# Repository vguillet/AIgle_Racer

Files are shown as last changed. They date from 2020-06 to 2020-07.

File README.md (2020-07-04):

# AIgle Racer Project

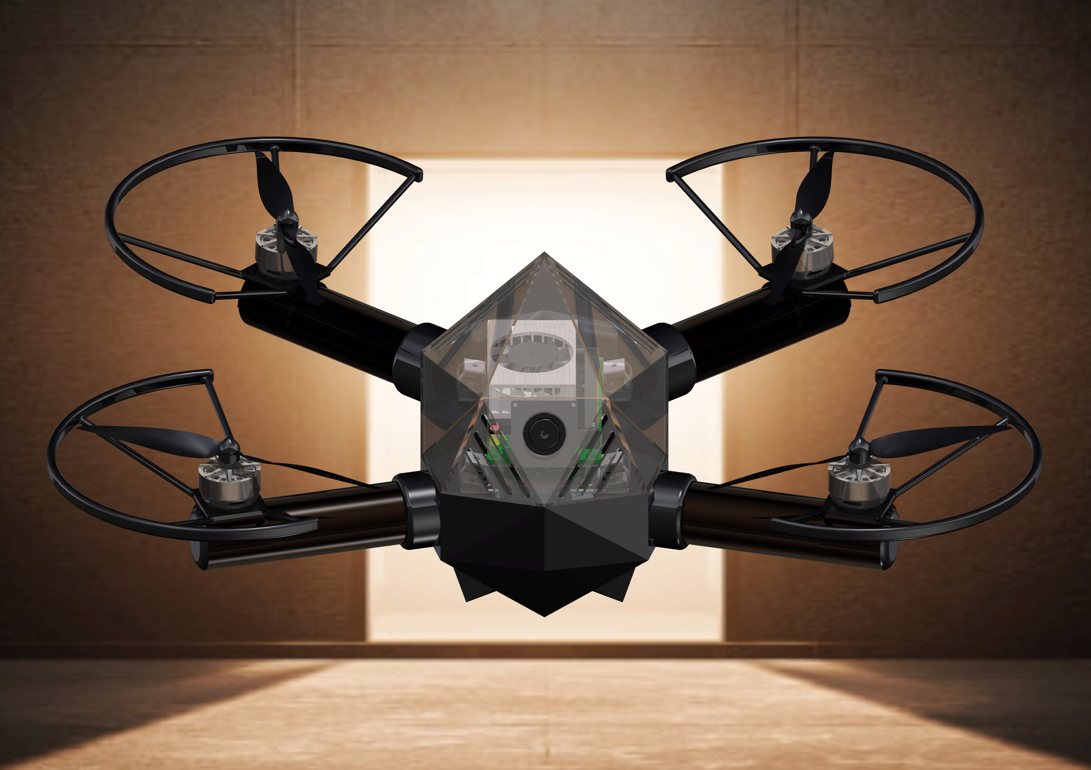
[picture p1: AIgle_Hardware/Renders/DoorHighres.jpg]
cover


> This project was developed during the 2019-2020 Fall DSE as part of the **TU Delft Aerspace Engineering Bachelor**.

> This project was undertaken with the intention of paving the way to future drone racing endeavor, and facilitate AI research and development.

> The design team consists of eleven Bachelor students working full time for 10 weeks. 

Drone racing has gathered increasing attention and interest in the past few years, establishing itself as a sport on par with more traditional ones such as Formula 1. A subset of it, autonomous drone racing, has been growing rapidly in popularity, recently capturing the interest of both the industry, the general public, and the scientific community. Since its beginning in 2016 with the IROS Autonomous Drone Race, the number of competitions have expanded, with more industry players such as the Drone Racing League (DRL) hosting its own competition in 2019, to fully virtual drone races being held by NeurIPS (also in 2019). 

The essence of these competition has however remained the same. Teams compete to develop the most effective software to pilot a standardised drone as quickly as possible over a given circuit. The drone being standardised is a critical aspect of the competition, as it ensures that the software is the sole deciding factor. During the DRL races, the competition host provided the drones competitors would be flying, ensuring this way that no drone had a mechanical advantage over its opponents. This however brings about a number of issues. The cost of hosting a competition goes up drastically, as the cost of producing, maintaining, and repairing the drones then becomes the responsibility of the host. It also means competitors would not be able to effectively test, adjust, and optimise their algorithms prior to the race, reducing the teams' potential ability to compete. In an effort to alleviate these issues, group 19 of the TU Delft 2020 DSE aims to propose an open-source hardware solution for race organizers and teams to be used in future autonomous drone racing competitions. The end goal of the project is to facilitate a worldwide collaboration on the development of artificial intelligence in agile autonomous drone flight. 

This repository contains all the information and results necessary to get started with the AIgle Racer platform. 

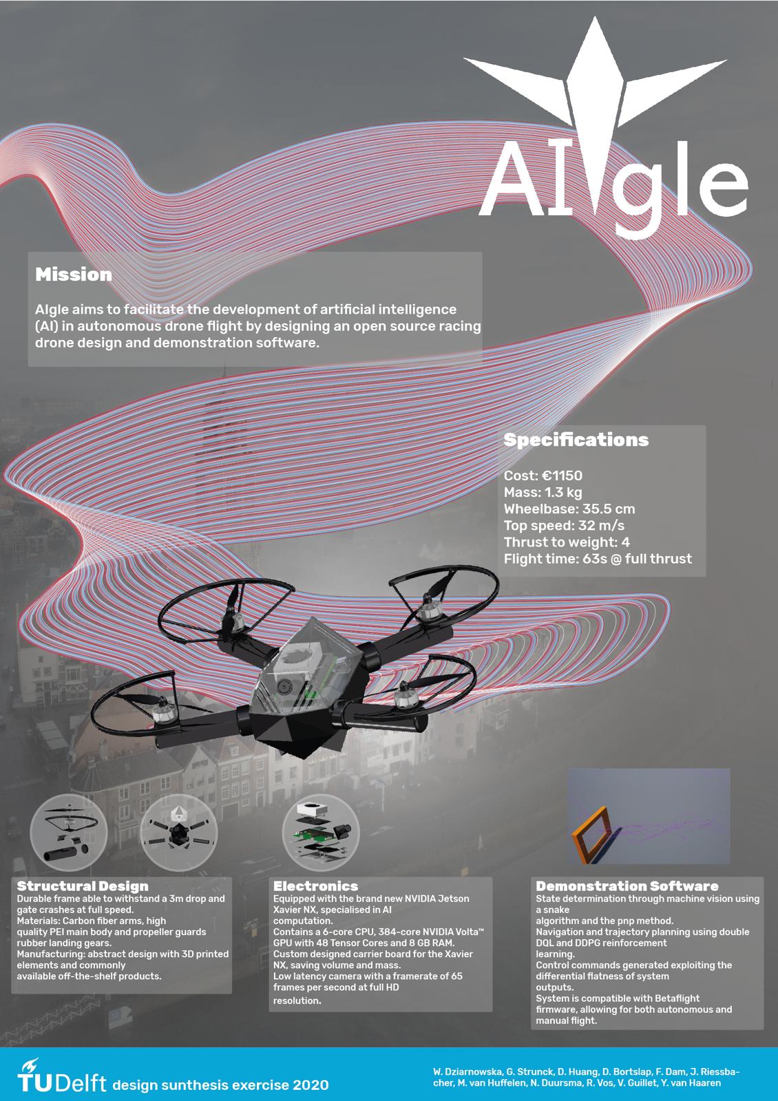
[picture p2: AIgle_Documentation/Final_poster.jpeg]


## AIgle Documentation

The AIgle Racer is documented in four distinct reports, each compiled at various stages of progress of the project.
  - Project plan: Depicts the initial organisation of the project
  - Baseline report: Describes the structuration of the research and development based on preliminary research,
  - Mid-term report: Explains the concepts elaboration and evaluation
  - Final report: Contains the detailed design, with the fully developed concept and instructions based on in-depth research.

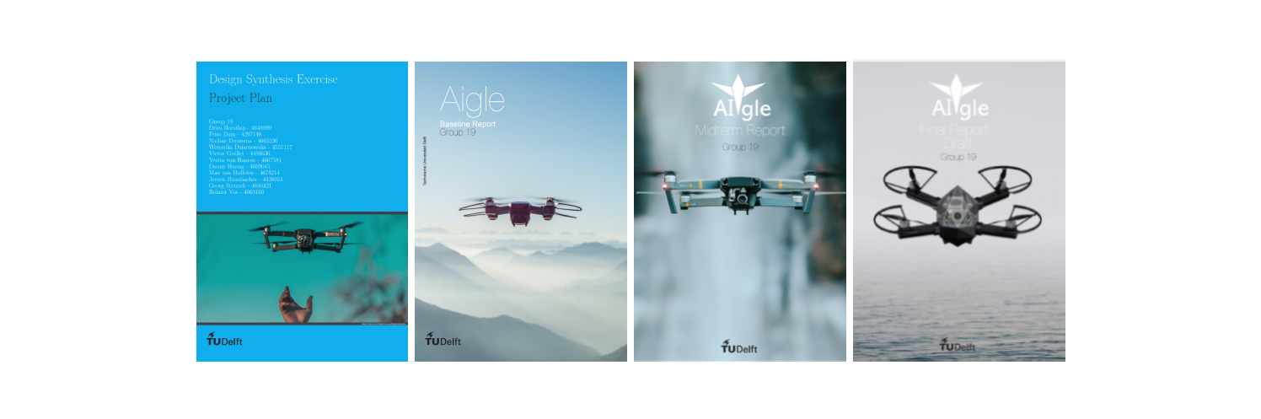
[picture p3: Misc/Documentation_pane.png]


## AIgle Hardware
The AIgle hardware folder contains all the information necessary for the production and assembly of the AIgle drone. To guide and facilitate the production, the following are provided:

  - Parts lists
  - 3D Catia models
  - Custom PCB diagrams and description
  
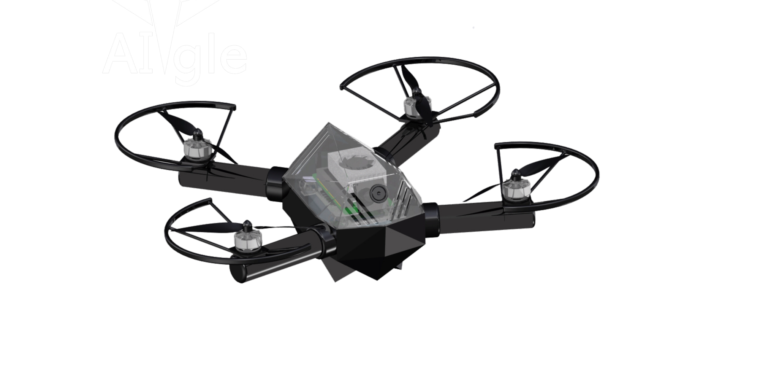
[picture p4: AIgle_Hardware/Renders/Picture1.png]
  

## AIgle Software
> Note: The AIgle demonstration software can be found in AIgle_Project/src

The AIgle Project src file contains all the demonstrations software provided to act as a baseline for building autonomous racing software to use with the AIgle racer platform. A general suggested pipeline is available in the documentation along with the result of research performed on the various methods and approach demonstrated.
  - Machine Vision & State estimation: Focus on retrieving and processing sensor data to get an estimate of the position of the drone in 3D space
  - Navigation: Focus on determining the path and trajectories to be followed by the drone during the race.
  
    Algorithms available: **DDQN**, **DDPG**
    
    The navigation uses [Airsim](https://github.com/microsoft/AirSim) as training and testing environment
    
  - Control & stability: Focus on translating the desired drone movement (control position, velocities, attitude) into commands (subsequenctly sent to an electronic speed controller) 

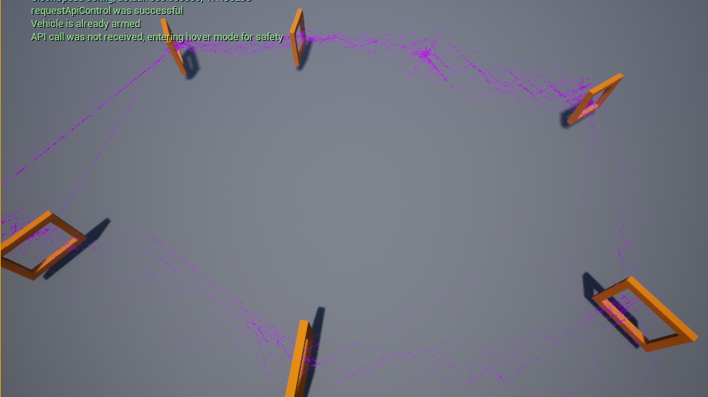
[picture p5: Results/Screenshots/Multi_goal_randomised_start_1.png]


## AIgle Concept Development Tools
The concept evelopment tool folder contains the code which was used for desiging and sizing the drone. This includes:
  - Propulsion: Contains the tools used to obtain suitable battery/motor/propelor triplets based on different input criterias. Vertification code is also included, to be used with [eCalc](https://ecalc.ch/xcoptercalc.php)
  - Structures:

## Acknowledgement
The group would like to extend special thanks to Ir. C. De Wagter for his tremendous insight into drone racing, and for sharing his knowledge and experience in drone racing design. The group would also like to thank B. Mercier and Y. Zhang for their valuable advices and help during the design phase, and D. Martini for his important input throughout the project. The tutors and coaches have been present throughout the entire development of the project, and their contribution has proven essential to its success.

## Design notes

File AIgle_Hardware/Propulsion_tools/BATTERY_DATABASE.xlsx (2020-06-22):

Battery | S_type | Capacity [mAh] | Weight [g] | Predicted weight [g] | Difference^2 | Cost ($) | Predicted cost [g] | Difference^2 | C-rating | Amps (=Cap*C) | Note | Source
1 | 4S | 2600 | 273 | 281.04 | 64.6416 | 36.06 | 27.668 | 70.425664 | 80 | 208 | From UK | https://www.hobbyrc.co.uk/gnb-2600mah-4s-80c-lipo-battery
2 | 4S | 3000 | 324 | 313 | 121 | 22.66 | 30.48 | 61.1524 | 30 | 90 |  | https://www.banggood.com/nl/ZOP-Power-14_8V-3000mah-30C-4S-Lipo-Battery-XT60-Plug-for-RC-Quadcopter-p-1237191.html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
3 | 4S | 2600 | 298 | 281.04 | 287.6416 |  | 27.668 | 765.518224 | 80 | 208 | No price info | https://www.amazon.com/RoaringTop-Battery-2600mAh-14-8V-Airplane/dp/B01LYZQE5S
4 | 4S | 2200 | 247 | 249.08 | 4.3264 | 31.06 | 24.856 | 38.489616 | 110 | 242 | From UK | https://www.hobbyrc.co.uk/gnb-2200mah-4s-110c-lipo-battery
5 | 4S | 4000 | 435 | 392.9 | 1772.41 | 34.61 | 37.51 | 8.41 | 60 | 240 |  | https://www.banggood.com/nl/ZOP-Power-14_8V-4000mAh-4S-60C-Lipo-Battery-XT60-Plug-p-1104628.html?gpla=1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

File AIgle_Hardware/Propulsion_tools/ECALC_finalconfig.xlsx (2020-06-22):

eCalc - Multicopter Calculator all data without guarantee - Accuracy: /-15%
Project Name |  | FINALCONFIG
Battery |  | custom
Configuration: |  | 4S1P
Load: | C | 44.70
Voltage: | V | 13.44
Rated Voltage: | V | 14.80
Energy: | Wh | 53.28
Total Capacity: | mAh | 3600
max. discharge: |  | 80%
Used Capacity: | mAh | 2880
min. Flight Time: | min | 1.1
Mixed Flight Time: | min | 5.8
Hover Flight Time: | min | 9.7
Weight: | g | 352
 | oz | 12.4
Controller |  | custom
Current: | A cont. | 45
 | A max | 45
Weight: | g | 4.5
 | oz | 0.2
Accessories
Current drain: | A | 2
Weight: | g | 237
 | oz | 8.4
Motor @ Maximum |  | EMAX Eco 2306-2400 (2400)
Gear Ratio: | : 1 | 1
Weight: | g | 28
 | oz | 1
Current: | A | 39.73
Voltage: | V | 13.20
Revolutions*: | rpm | 26806
electric Power: | W | 524.3
mech. Power: | W | 424.6
Efficiency: | % | 81.0
est. Temperature: | °C | 64
 | °F | 147
Motor @ Hover
Propeller |  | APC Electric E (0°) 6" x 4"
# Blades: |  | 2
avail.Thrust @ | @
 | @
Current: | A | 3.95
Voltage: | V | 15.41
Revolutions*: | rpm | 11765
Throttle (log): | % | 22
Throttle (linear): | % | 35
Power-Weight: | W/kg | 198.6
 | W/lb | 90.1
Efficiency: | % | 82.3
specific Thrust: | g/W | 5.13
 | oz/W | 0.18
est. Temperature: | °C | 29
 | °F | 84
Total Drive
Drive Weight: | g | 530
 | oz | 18.7
Power-Weight: | W/kg | 1681.5
 | W/lb | 762.7
Thrust-Weight: | : 1 | 4.2
Current @ Hover: | A | 15.79
P(in) @ Hover: | W | 247.7
P(out) @ Hover: | W | 200.2
Efficiency @ Hover: | % | 80.8
Current @ max: | A | 158.91
P(in) @ max: | W | 2493.0
P(out) @ max: | W | 1698.3
Efficiency @ max: | % | 68.1
Multicopter
# of Rotors: |  | 4 - flat
All-up Weight: | g | 1247
 | oz | 44
add. Payload: | g | 3229
 | oz | 113.9
max Tilt: | ° | 74
max. Speed: | km/h | 166
 | mph | 103.1
est. Range: | m | 4374
 | mi | 2.72
est. rate of climb: | m/s | 28.4
 | ft/min | 5591
Total Disc Area: | dm² | 7.30
 | in² | 113.15
with Rotor fail: |  | uncontrolable
Remarks: |  | 0
(c) by Solution for All - 7.20.010, 13.5.2020

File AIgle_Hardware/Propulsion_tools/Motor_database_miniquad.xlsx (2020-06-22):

Name | TESTED_KV | motor_weight(g) | Prop_Tested(100) | T_Max(g) | T_avg_max(g) | I_max(A) | I_avg_max(A) | Volt_avg_min | Volt_max | RPM_max | RPM_min | RPM_avg_max | Watts | T/W(g/W) | Prop(IDLE) | Thrust(g)(IDLE) | Amps(IDLE) | Volts(IDLE) | RPMs(IDLE) | Watts(IDLE) | T/W(g/W)(IDLE)
Karearea Toa 2207 2650kv | 2700 | 33.8 | HQ v1s 5x4x3 | 1508.00 | 1480.00 | 161.52 | 41.82 | 15.45 | 16.16 | 36014.00 | 34423.00 | 34925.00 | 646.00 | 2.30 | HQ v1s 5x4x3 | 46.00 | 0.99 | 16.13 | 6298.00 | 16.00 | 2.90
Karearea Toa 2207 2650kv | 2700 | 33.8 | Lumenier 5x4.5 | 1552.00 | 1537.00 | 181.45 | 46.00 | 15.35 | 16.16 | 35714.00 | 33094.00 | 33552.00 | 706.00 | 2.20 | Lumenier 5x4.5 | 48.00 | 0.85 | 16.12 | 6311.00 | 14.00 | 3.50
Karearea Toa 2207 2650kv | 2700 | 33.8 | DAL Cyclone 5x4x3 | 1556.00 | 1537.00 | 175.11 | 46.66 | 15.37 | 16.16 | 34843.00 | 32840.00 | 33378.00 | 717.00 | 2.10 | DAL Cyclone 5x4x3 | 45.00 | 0.96 | 16.13 | 6326.00 | 15.00 | 2.90
Karearea Toa 2207 2650kv | 2700 | 33.8 | HQ 5x4x3GF | 1608.00 | 1595.00 | 180.16 | 48.57 | 15.34 | 16.16 | 34843.00 | 32345.00 | 32867.00 | 745.00 | 2.10 | HQ 5x4x3GF | 59.00 | 1.08 | 16.13 | 6289.00 | 17.00 | 3.40
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

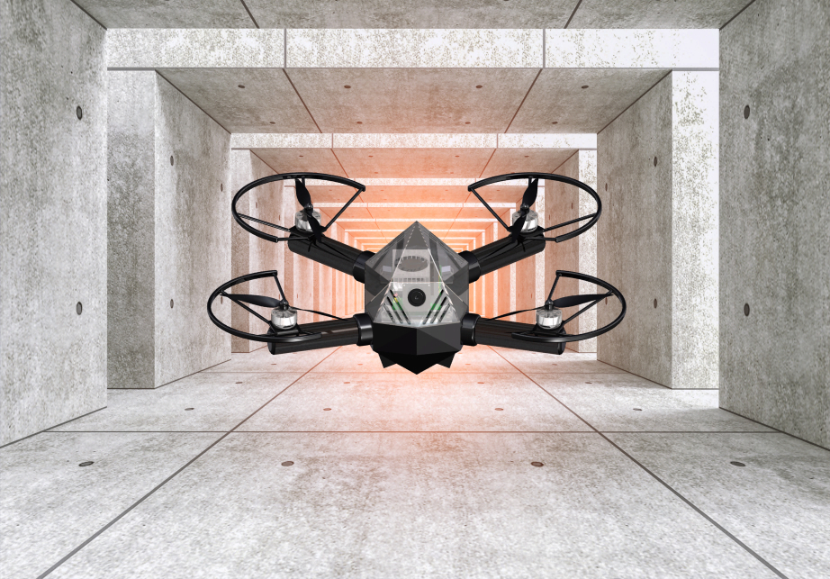
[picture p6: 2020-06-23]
AIgle_Hardware/Renders/Gates3.jpg

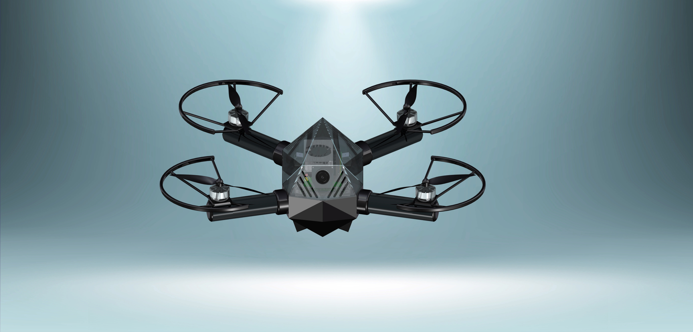
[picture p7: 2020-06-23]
AIgle_Hardware/Renders/Grey2.jpg

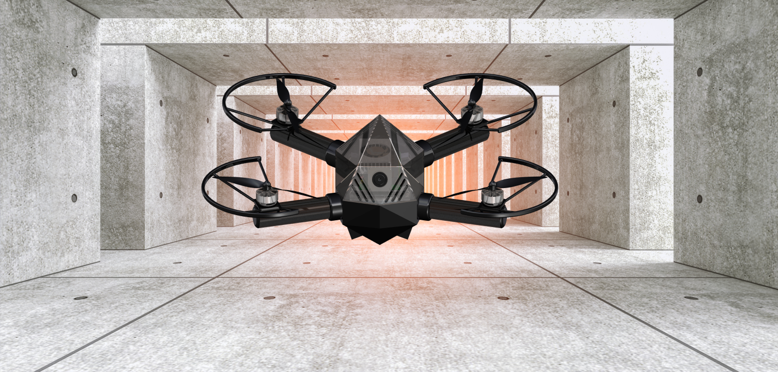
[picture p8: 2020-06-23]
AIgle_Hardware/Renders/Gates.png

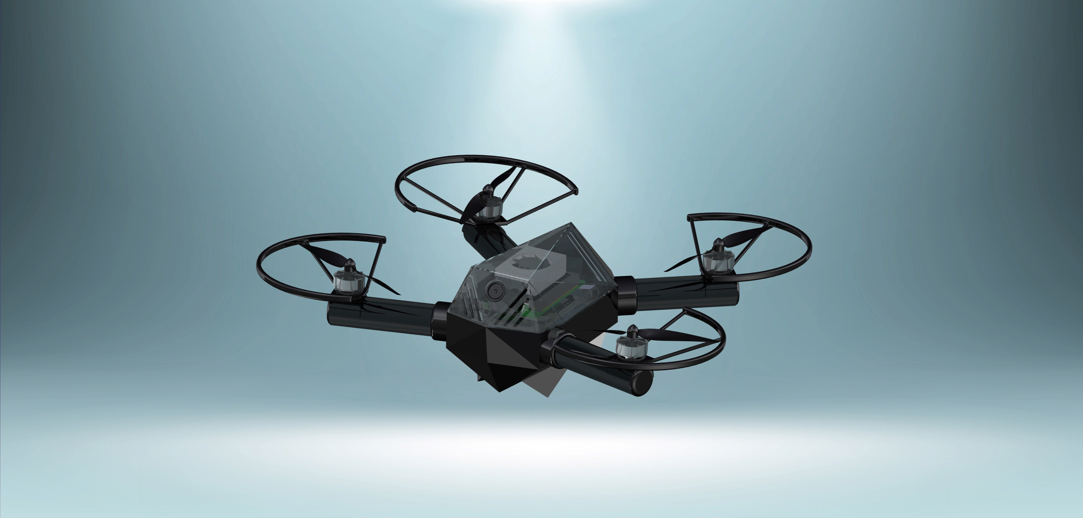
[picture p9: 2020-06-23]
AIgle_Hardware/Renders/Grey.jpg

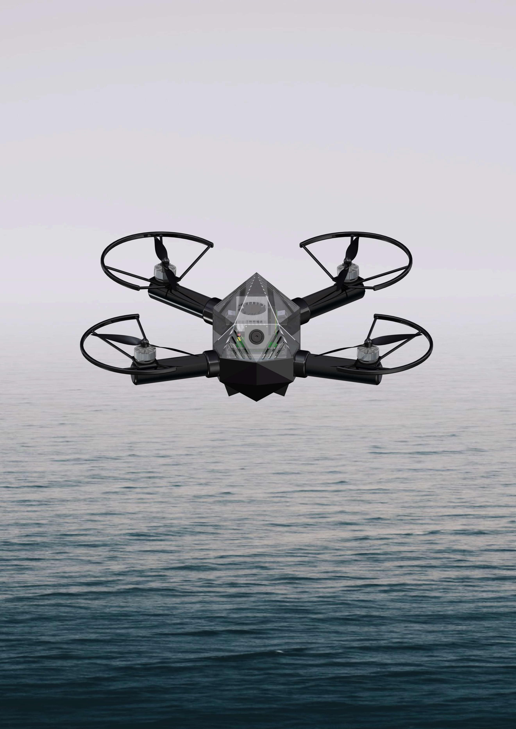
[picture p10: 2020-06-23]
AIgle_Hardware/Renders/Renderfront.jpg

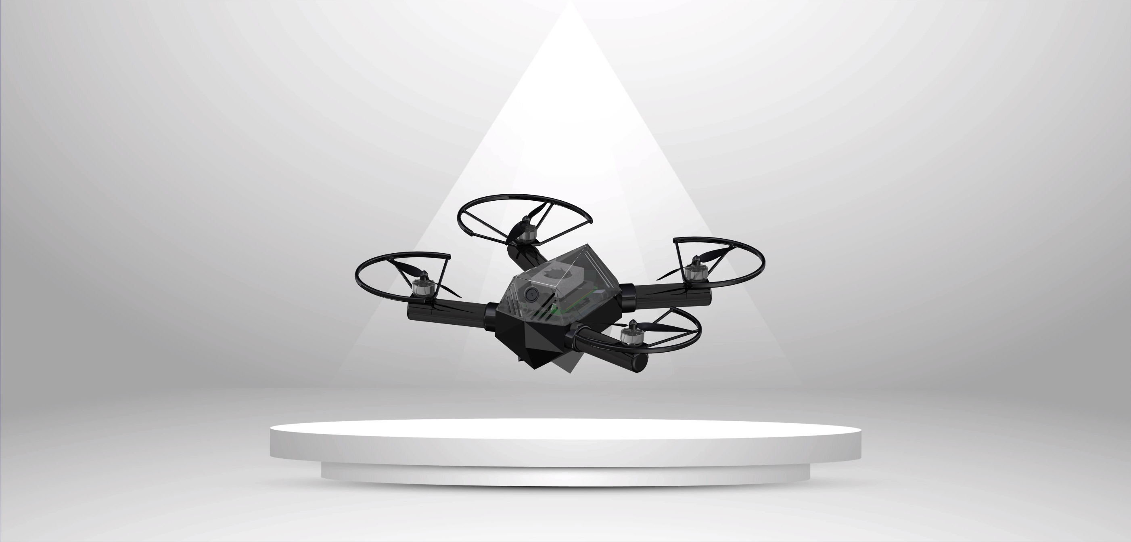
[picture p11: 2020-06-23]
AIgle_Hardware/Renders/platform.jpg

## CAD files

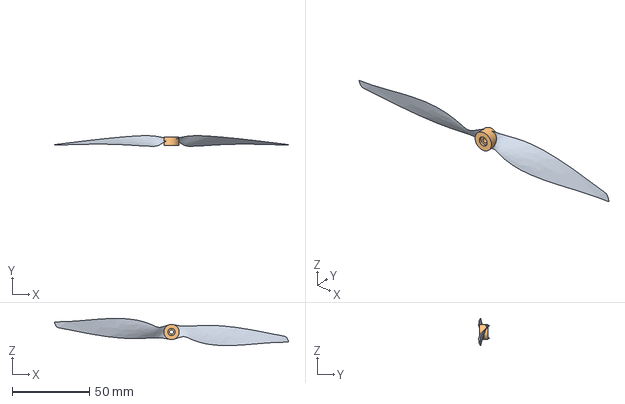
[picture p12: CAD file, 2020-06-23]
AIgle_Hardware/Catia_Models/APC12x6EPPropv1scaled v1.step
151.9 x 6.87 x 17.7 mm

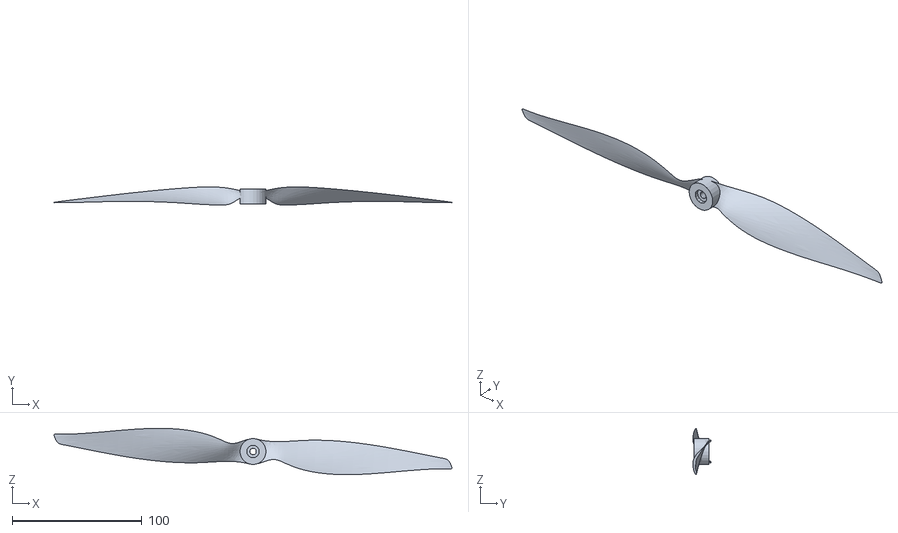
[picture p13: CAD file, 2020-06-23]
AIgle_Hardware/Catia_Models/APC12x6EPProp v1.stl
306.6 x 14.0 x 35.7

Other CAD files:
AIgle_Hardware/Catia_Models/Arm.CATPart
AIgle_Hardware/Catia_Models/AssemblyExploded.CATProduct
AIgle_Hardware/Catia_Models/AssemblyFinal.CATProduct
AIgle_Hardware/Catia_Models/PropDop.CATPart
AIgle_Hardware/Catia_Models/PropGuards.CATPart
AIgle_Hardware/Catia_Models/Propeller.CATPart
AIgle_Hardware/Catia_Models/Reference.CATPart
AIgle_Hardware/Catia_Models/Symmetry of Arm.CATPart
AIgle_Hardware/Catia_Models/Symmetry of Dopje.CATPart
AIgle_Hardware/Catia_Models/Symmetry of LandingGear.CATPart
AIgle_Hardware/Catia_Models/Symmetry of MotorMount.CATPart
AIgle_Hardware/Catia_Models/Symmetry of Product4.CATProduct
AIgle_Hardware/Catia_Models/Symmetry of PropGuards.CATPart

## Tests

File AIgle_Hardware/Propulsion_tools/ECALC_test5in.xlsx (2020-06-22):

eCalc - Multicopter Calculator all data without guarantee - Accuracy: /-15%
Project Name |  | VERI1WIN5in | VERI2WIN5in | VERI3WIN5in
Battery |  | LiPo 3000mAh - 65/100C | LiPo 3000mAh - 65/100C | LiPo 4000mAh - 55/80C
Configuration: |  | 4S1P | 4S1P | 4S1P
Load: | C | 39.77 | 44.02 | 39.05
Voltage: | V | 13.83 | 13.63 | 13.81
Rated Voltage: | V | 14.80 | 14.80 | 14.80
Energy: | Wh | 44.4 | 44.4 | 59.2
Total Capacity: | mAh | 3000 | 3000 | 4000
max. discharge: |  | 80% | 80% | 80%
Used Capacity: | mAh | 2400 | 2400 | 3200
min. Flight Time: | min | 1.2 | 1.1 | 1.2
Mixed Flight Time: | min | 5.7 | 5.6 | 6.8
Hover Flight Time: | min | 9.6 | 9.5 | 11.9
Weight: | g | 336 | 336 | 432
 | oz | 11.9 | 11.9 | 15.2
Controller |  | custom | custom | custom
Current: | A cont. | 45 | 45 | 45
 | A max | 45 | 45 | 45
Weight: | g | 4.5 | 4.5 | 4.5
 | oz | 0.2 | 0.2 | 0.2
Accessories
Current drain: | A | 2 | 2 | 2
Weight: | g | 185 | 185 | 185
 | oz | 6.5 | 6.5 | 6.5
Motor @ Maximum |  | Cobra CP-2207-2300 (2300) | T-Motor F60 PRO III KV2500 (2500) | iFlight XING-E X2306-2450KV (2450)
Gear Ratio: | : 1 | 1 | 1 | 1
Weight: | g | 36 | 35 | 33
 | oz | 1.3 | 1.2 | 1.2
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

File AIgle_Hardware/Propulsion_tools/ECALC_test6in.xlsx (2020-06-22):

eCalc - Multicopter Calculator all data without guarantee - Accuracy: /-15%
Project Name |  | VERI1WIN6in | VERI2WIN6in
Battery |  | LiPo 3000mAh - 65/100C | LiPo 4200mAh - 55/80C
Configuration: |  | 4S1P | 4S1P
Load: | C | 47.75 | 41.63
Voltage: | V | 13.45 | 13.66
Rated Voltage: | V | 14.80 | 14.80
Energy: | Wh | 44.4 | 62.16
Total Capacity: | mAh | 3000 | 4200
max. discharge: |  | 80% | 80%
Used Capacity: | mAh | 2400 | 3360
min. Flight Time: | min | 1.0 | 1.2
Mixed Flight Time: | min | 5.7 | 7.0
Hover Flight Time: | min | 10.4 | 12.5
Weight: | g | 336 | 452
 | oz | 11.9 | 15.9
Controller |  | custom | custom
Current: | A cont. | 40 | 45
 | A max | 40 | 45
Weight: | g | 4.5 | 4.5
 | oz | 0.2 | 0.2
Accessories
Current drain: | A | 2 | 2
Weight: | g | 185 | 185
 | oz | 6.5 | 6.5
Motor @ Maximum |  | Cobra CP-2207-2450 (2450) | iFlight XING-E X2306-2450KV (2450)
Gear Ratio: | : 1 | 1 | 1
Weight: | g | 36 | 33
 | oz | 1.3 | 1.2
Current: | A | 35.31 | 43.21
Voltage: | V | 13.24 | 13.40
Revolutions*: | rpm | 28496 | 27393
electric Power: | W | 467.6 | 579.0
mech. Power: | W | 385.3 | 457.4
Efficiency: | % | 82.4 | 79.0
est. Temperature: | °C | 54 | 73
 | °F | 129 | 163
Motor @ Hover
Propeller |  | APC MultiRotor MR (0°) 6" x 3" | APC MultiRotor MR (0°) 6" x 4"
# Blades: |  | 2 | 2
avail.Thrust @ | @
 | @
Current: | A | 2.96 | 3.53
Voltage: | V | 15.45 | 15.48
Revolutions*: | rpm | 11669 | 11185
Throttle (log): | % | 20 | 19
Throttle (linear): | % | 33 | 33
Power-Weight: | W/kg | 183.4 | 196.6
 | W/lb | 83.2 | 89.2
Efficiency: | % | 80.8 | 79.4
specific Thrust: | g/W | 5.54 | 5.16
 | oz/W | 0.2 | 0.18
est. Temperature: | °C | 28 | 29
 | °F | 82 | 84
Total Drive
Drive Weight: | g | 548 | 662
 | oz | 19.3 | 23.4
Power-Weight: | W/kg | 1846.6 | 2054.8
 | W/lb | 837.6 | 932
Thrust-Weight: | : 1 | 4.7 | 4.8
Current @ Hover: | A | 11.84 | 14.13
P(in) @ Hover: | W | 185.7 | 221.6
P(out) @ Hover: | W | 147.9 | 173.6
Efficiency @ Hover: | % | 79.6 | 78.3
Current @ max: | A | 141.24 | 172.84
P(in) @ max: | W | 2215.8 | 2711.5
P(out) @ max: | W | 1541.0 | 1829.8
Efficiency @ max: | % | 69.5 | 67.5
Multicopter
# of Rotors: |  | 4 - flat | 4 - flat
All-up Weight: | g | 1013 | 1127
 | oz | 35.7 | 39.8
add. Payload: | g | 3066 | 3528
 | oz | 108.1 | 124.4
max Tilt: | ° | 75 | 75
max. Speed: | km/h | 142 | 171
 | mph | 88.2 | 106.2
est. Range: | m | 3798 | 5446
 | mi | 2.36 | 3.38
est. rate of climb: | m/s | 23.5 | 30.3
 | ft/min | 4626 | 5965
Total Disc Area: | dm² | 7.30 | 7.30
 | in² | 113.15 | 113.15
with Rotor fail: |  | uncontrolable | uncontrolable
Remarks: |  | 0 | 0
(c) by Solution for All - 7.20.010, 13.5.2020

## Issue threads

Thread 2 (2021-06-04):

Setup AirSim Environment

brunopinto900, 2021-06-04:
Hello,

I am developing an autonomous drone racing and using AirSim as the simulator. How do i setup the environment (the racing gates + Blocks) using this repository?

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

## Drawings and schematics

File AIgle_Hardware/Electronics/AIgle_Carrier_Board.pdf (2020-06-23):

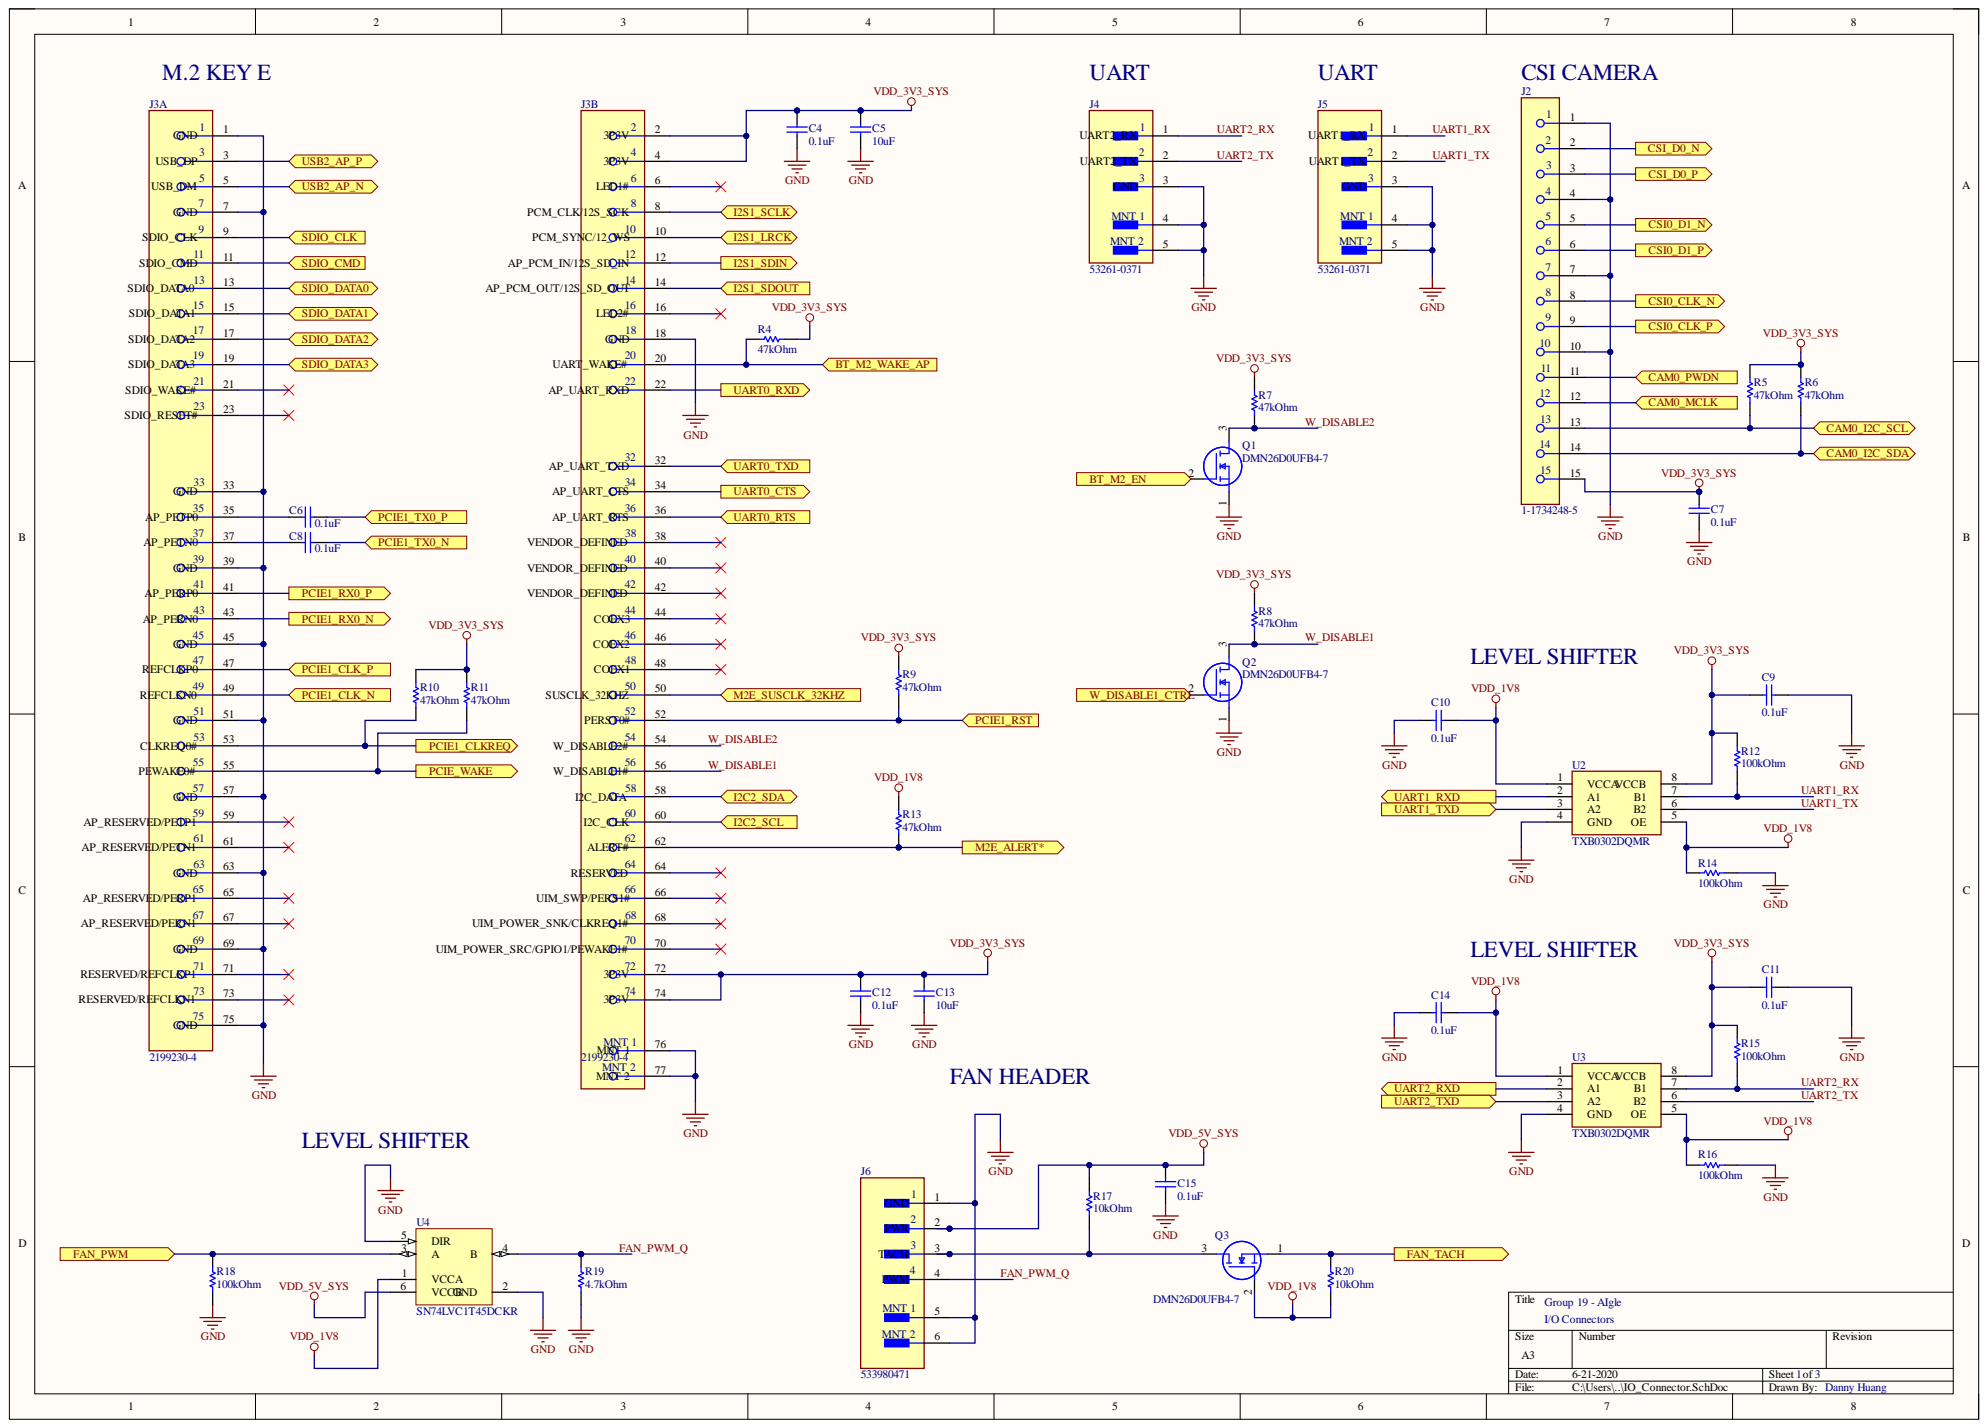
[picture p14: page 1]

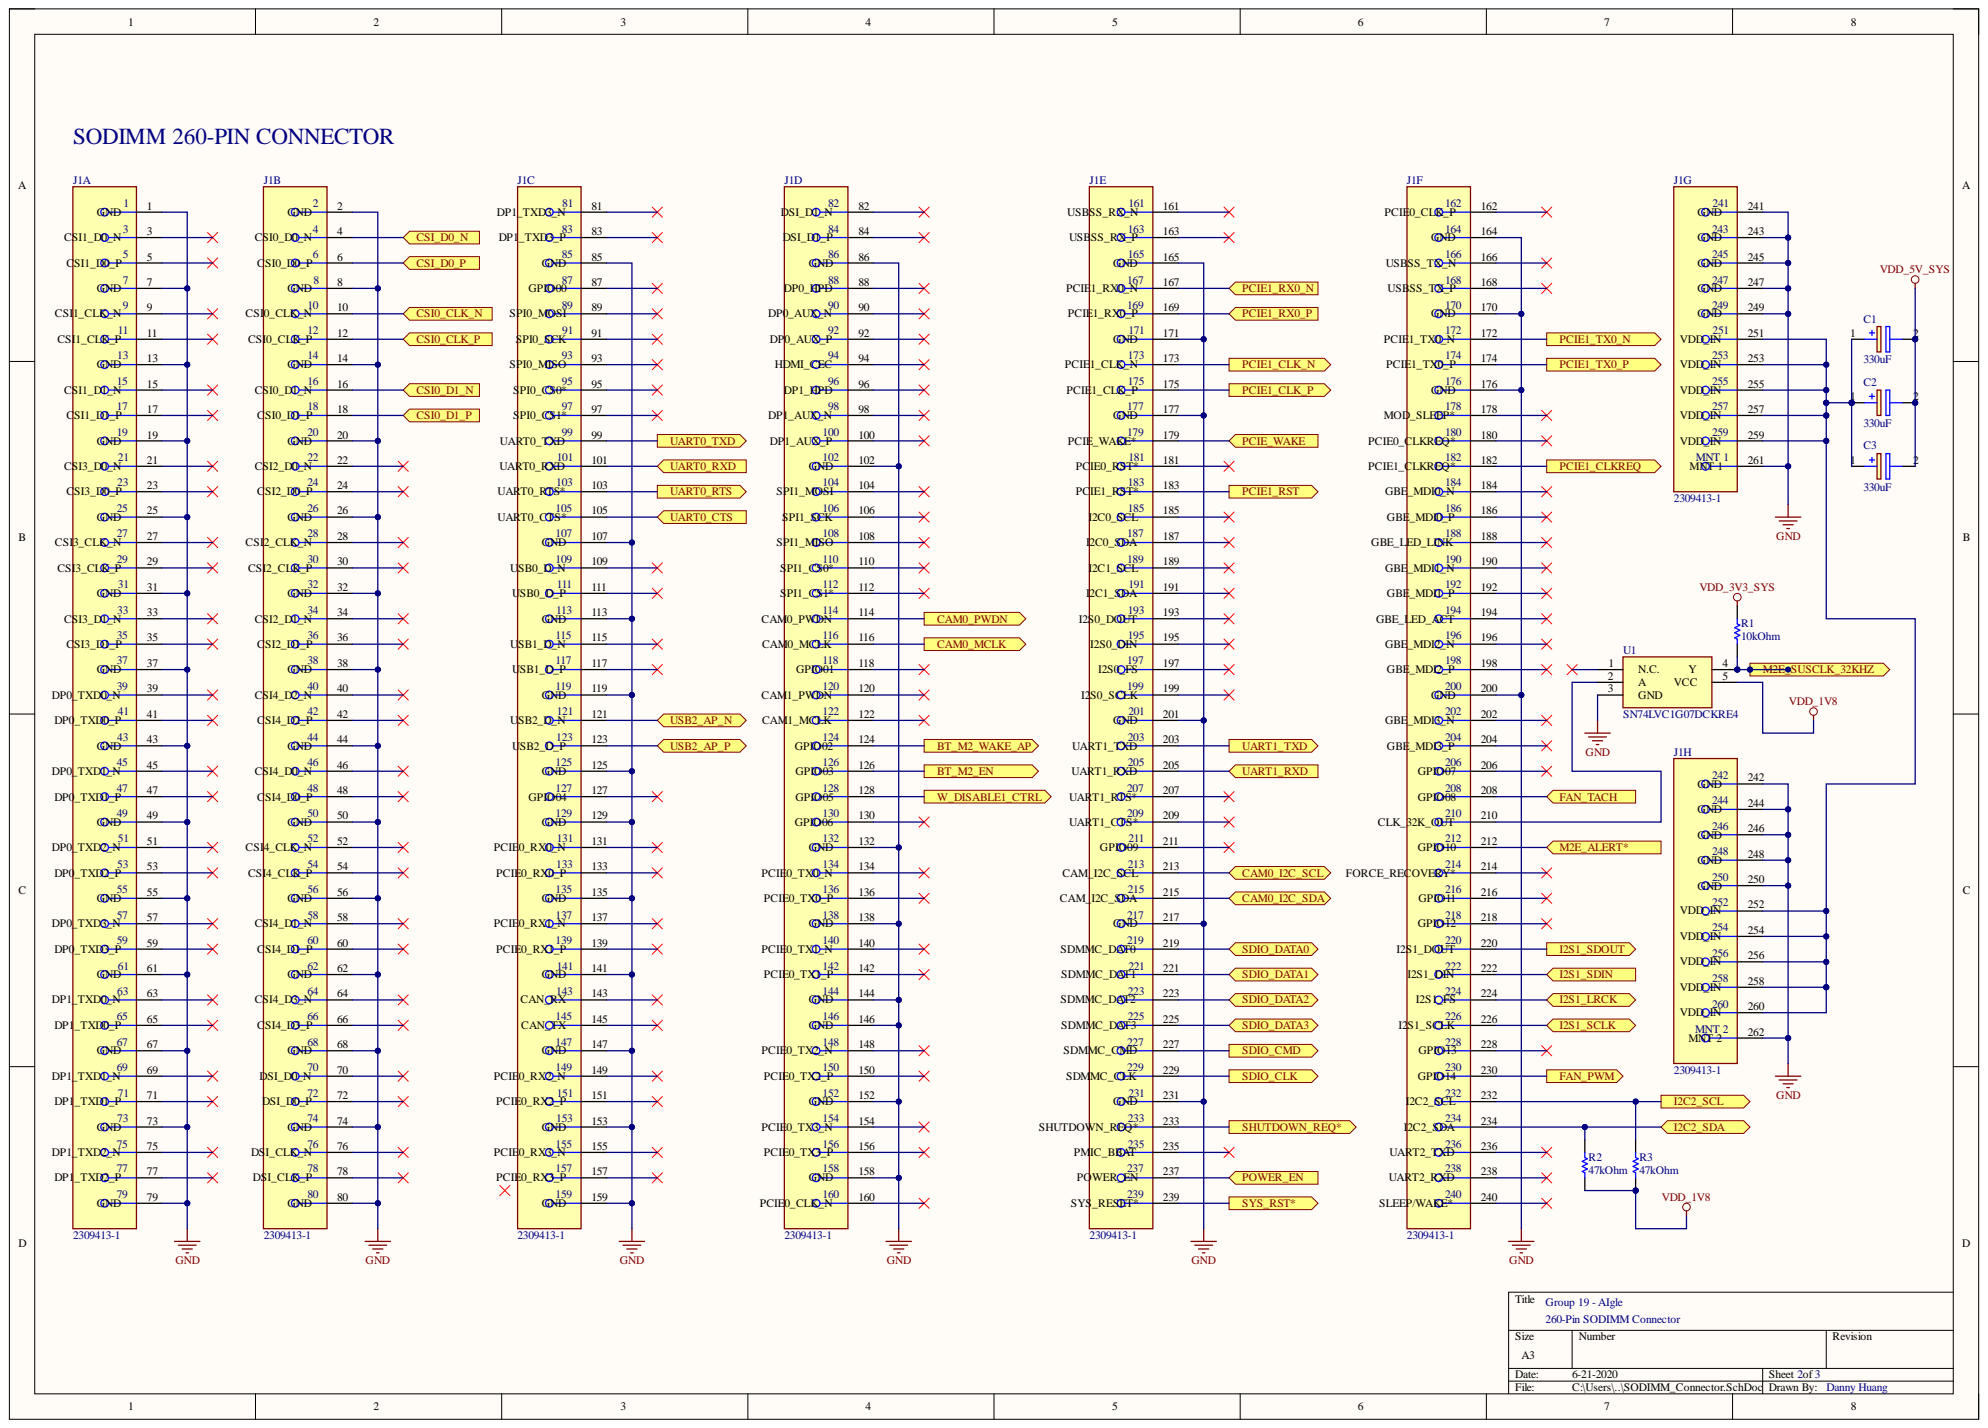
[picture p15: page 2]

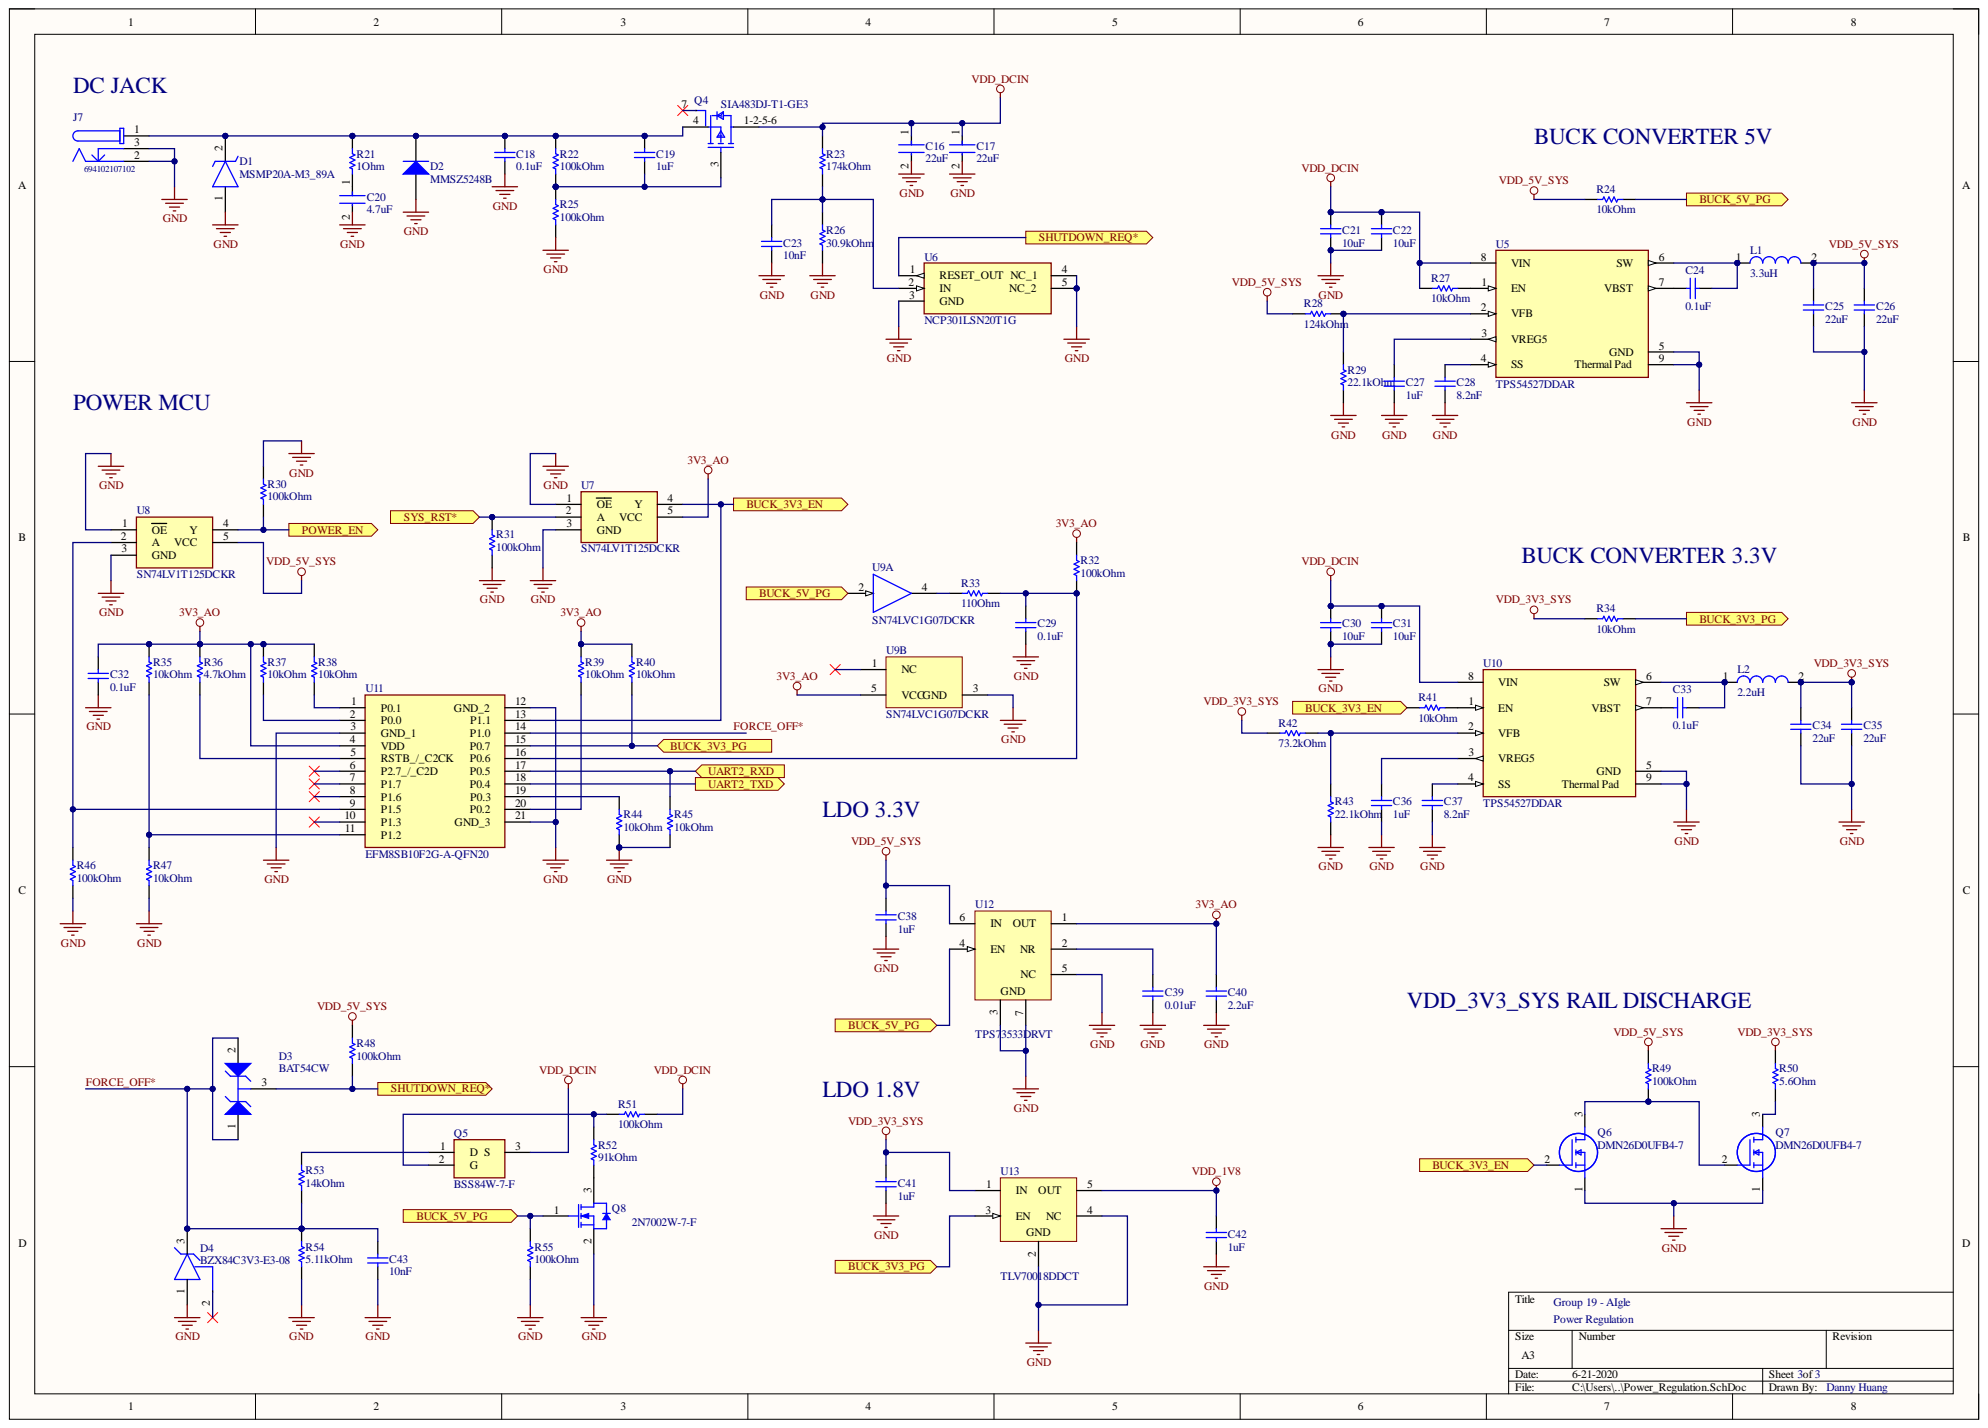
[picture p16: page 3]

Comment | Description | Designator | Footprint | LibRef | Quantity
330uF | Capacitor Polarised | C1, C2, C3 | CAPPM3528X210N | T520B337M006ATE04
0.1uF | | C4, C6, C7, C8, C9, C10, C11, C12, C14, C15, C18, C24, C29, C32, C33 | CAPC1005X55X30NL0 5T10 | CMP-2008-03087-1 | 15
10uF | | C5, C13, C21, C22, C30, C31 | CAPC1608X90X35NL1 0T15 | CMP-2006-02792-1 | | 6
22uF | CAP CER 22UF 25V X5R 0805 | C16, C17 | FP-GRM21-0_2-MFG | CMP-06035-000059-1 | | 2
1uF | | C19 | CAPC1608X90X35LL10 T15 | CMP-2006-02459-1 | | 1
4.7uF | CAP CER 4.7UF 6.3V X5R 0603 | C20 | FP-C0603-CG-MFG | CMP-03020-024641-1 | | 1
10nF | | C23, C43 | CAPC1005X55X30NL0 5T10 | CMP-2008-03072-1 | | 2
22uF | Chip Capacitor, 22 uF, +/- 20%, 6.3 V, -55 to 85 degC, 1608 (0603 Metric), RoHS, Tape and Reel | C25, C26, C34, C35 | CAPC1608X100X20ML 10 | CMP-2000-05440-1 | | 4
1uF | | C27, C36, C38, C41, C42 | CAPC1005X60X30ML0 5T10 | CMP-2008-02075-1 | | 5
8.2nF | | C28, C37 | CAPC1005X55X30ML0 5T10 | CMP-2008-03262-1 | | 2
0.01uF | | C39 | CAPC1005X55X30LL05 T10 | CMP-2008-03076-1 | | 1
2.2uF | | C40 | CAPC1005X60X30NL0 5T10 | CMP-2008-02055-1 | | 1
MSMP20A-M3_89A | TVS Diode (Uni-directional) | D1 | MICROSMP(ESMP) | MSMP20A-M3_89A | | 1
MMSZ5248B | Zener Diode, 18 V, -55 to 150 degC, 2-Pin SOD-123, RoHS, Tape and Reel | D2 | FAIR-SOD-123-2_V | CMP-2000-06744-1 | | 1
BAT54CW | SOT-323 Plastic-Encapsulated Diode | D3 | NXP-SOT323-3_L | CMP-0417-00001-1 | | 1
BZX84C3V3-E3-08 | DIODE ZENER 3.3V 300MW SOT23 | D4 | FP-6_541-5014_01-4-MFG | CMP-02541-000017-1 | | 1
2309413-1 | DDR4 SODIMM 260P 9.2H STD | J1 | FP-2309413-1-MFG | CMP-03356-000001-1 | | 1
1-1734248-5 | CONN FPC VERT 15POS 1.00MM SMD | J2 | FP-1-1734248-5-MFG | CMP-03368-000001-1 | | 1
2199230-4 | CONN FEMALE 67POS 0.020 GOLD | J3 | FP-2199230-4-MFG | CMP-03365-000002-1 | | 1
53261-0371 | CONN HEADER SMD R/A 3POS 1.25MM | J4, J5 | FP-53261-0371-MFG | CMP-04776-000071-1 | | 2
533980471 | CONN HEADER SMD 4POS 1.25MM | J6 | FP-533980471-MFG | CMP-04776-000105-1 | | 1
694102107102 | DC Power Jack Connector Low Profile with 4 soldering pads & Pegs WR-DC, Male, Right Angled, SMT, 5 A, 18 V | J7 | 694102107102 | CMP-1502-00174-1 | | 1
3.3uH | Power Multilayer Inductor WE-PMI, L=3.30 µH | L1 | SMD 0806 | CMP-1392-00058-1 | | 1
2.2uH | Power Multilayer Inductor WE-PMI, L=2.20 µH | L2 | SMD 0805-Low profile | CMP-1392-00044-1 | | 1
DMN26D0UFB4-7 | MOSFET (N-Channel) | Q1, Q2, Q3, Q6, Q7 | DMN26D0UFB47 | DMN26D0UFB4-7 | | 5
SIA483DJ-T1-GE3 | MOSFET P-CH 30V 12A SC70-6 | Q4 | FP-C-07431-MFG | CMP-02550-000185-1 | | 1
BSS84W-7-F | Undefined or Miscellaneous | Q5 | SOT65P210X110-3N | BSS84W-7-F | | 1
2N7002W-7-F | N-Channel Enhancement Mode Field Effect Transistor, 60 V (VDS), 0.115 A (IDS), -55 to 150 degC, 3-Pin SOT323, RoHS, Tape and Reel | Q8 | DIOD-SOT323-3_V | CMP-2000-05568-1 | | 1
10kOhm | | R1, R17, R20, R24, R27, R34, R35, R37, R38, R39, R40, R41, R44, R45, R47 | RESC1005X40X25NL05 T05 | CMP-2002-08136-1, CMP-2002-08135-1 | 15
47kOhm | | R2, R3, R4, R5, R6, R7, R8, R9, R10, R11, R13 | RESC1005X40X25LL05 T05 | CMP-2002-00026-1 | 11
100kOhm | Chip Resistor, 100 KOhm, +/- 1%, 0.63 W, -55 to 155 degC, 0402 (1005 Metric), RoHS, Tape and Reel | R12, R14, R15, R16, R18, R22, R25, R30, R31, R32, R46, R48, R49, R51, R55 | RESC1005X40X25ML0 5T05 | CMP-2002-08123-2 | 15
4.7kOhm | | R19, R36 | RESC1005X40X25ML0 5T05 | CMP-2002-00053-1 | | 2
1Ohm | | R21 | RESC1005X40X25ML0 5T05 | CMP-2002-08342-1 | | 1
174kOhm | | R23 | RESC1005X40X25LL05 T05 | CMP-2002-08244-1 | | 1
30.9kOhm | | R26 | RESC1005X40X25LL05 T05 | CMP-2002-08508-1 | | 1
124kOhm | | R28 | RESC1005X40X25ML0 5T05 | CMP-2002-08173-1 | | 1
22.1kOhm | | R29, R43 | RESC1005X40X25ML0 5T05 | CMP-2002-08380-1 | | 2
110Ohm | | R33 | RESC1005X40X25LL05 T05 | CMP-2002-08151-1 | | 1
73.2kOhm | | R42 | RESC1005X40X25ML0 5T05 | CMP-2002-00203-1 | | 1
5.6Ohm | | R50 | RESC1005X40X25ML0 5T05 | CMP-2002-00563-1 | | 1
91kOhm | | R52 | RESC1005X40X25ML0 5T05 | CMP-2002-00271-1 | | 1
14kOhm | | R53 | RESC1005X40X25LL05 T05 | CMP-2002-08207-1 | | 1
5.11kOhm | | R54 | RESC1005X40X25LL05 T05 | CMP-2002-00117-1 | | 1
SN74LVC1G07DCKRE4 | Integrated Circuit | U1 | SOT65P210X110-5N | SN74LVC1G07DCKRE4 | | 1
TXB0302DQMR | Integrated Circuit | U2, U3 | SON40P120X180X40-8N | TXB0302DQMR | | 2
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

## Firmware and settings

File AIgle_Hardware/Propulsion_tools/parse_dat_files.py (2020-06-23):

import os
import numpy as np
import pandas as pd
import re
from io import StringIO
from IPython.display import display
import matplotlib.pyplot as plt
from mpl_toolkits.mplot3d import Axes3D
import math as m 
#scikit for regression
#%%################################################----------------- parameters (LIMITS) --------------------------###########################################
    ##### GENERAL #####
    #Theres a total of 520 propeller dat files: 5 to 7 inch are between range(343,417)
    #Vmph_req = 49.77 mph
    #Thrust total per psu =  2.4129594596135115 lbf
#dat_start = 343         # DO NOT TOUCH - this means it only starts looking from 5 inch props onwards
#dat_end = 361           # DO NOT TOUCH - end of 5 inch
dat_start = 361         # DO NOT TOUCH - start 6 inch
dat_end = 369           # DO NOT TOUCH - end 6 inch
    # 5 inch starts at index 343
    # 6 inch starts at index 367
    # 7 inch starts at index 385
    # 7 inch ends at index 416 so use 417
mass_estimate = 1314                                                # CONCEPT MASS ESTIMATE [g]
T_W_REQ = 4.0                                                       # Required thrust to weight ratio
T_W_toplim = 4.8                                                  #Top limit for thrust to weight ratio - ensure this is higher than the required!
n_motors = 4                                                        # amount of motors
v_free = 10.00                                                      # free stream velocity [m/s]
max_tilt = 7.4                                                       # max tilt angle [degrees]
v_axial = m.cos(m.radians(90-max_tilt))*v_free                      # speed hitting the propeller - axial velocity [m/s]
v_margin_mph = 2                                                    # margin in mile-per-hour [mph]

    ### bottom & top limits computations ###
v_axial_mph = 2.23694*v_axial                                       # speed hitting the propeller - axial velocity [mph]
v_axial_mph_top = v_axial_mph+v_margin_mph                          # TOP LIMIT speed hitting the propeller - axial velocity [mph] 
v_axial_mph_bot = v_axial_mph-v_margin_mph                          # bottom LIMIT speed hitting the propeller - axial velocity [mph] 
v_axial_top = v_axial_mph_top/2.23694                               # TOP LIMIT speed hitting the propeller - axial velocity [m/s] 
v_axial_bot = v_axial_mph_bot/2.23694                               # bottom LIMIT speed hitting the propeller - axial velocity [m/s] 
gram_to_lbf = 0.0022046226218488                                    # conversion from gram to pound force
thrust_per_m_gram = (mass_estimate*T_W_REQ)/n_motors                # thrust per motor required (bottom limit) in grams
thrust_per_m_lbf = thrust_per_m_gram*gram_to_lbf     # thrust per motor required (bottom limit) in grams
thrust_top_m_gram = (mass_estimate*T_W_toplim)/n_motors             # top limit thrust amount generated [g] - ensure this higher than bottom limit of thrust!
thrust_top_m_lbf = gram_to_lbf*thrust_top_m_gram                    # top limit thrust amount generated [lbf]
##############------- PROPELLER DATABASE RELATED ---------############### 
    #### PROP FILTER 1 PARAMETERS ####
Vbot = v_axial_mph_bot                                   # BOTTOM LIMIT OF AXIAL VELOCITY [MPH]   - if this doesnt matter choose a very low value!
Vtop = v_axial_mph_top                                   # TOP LIMIT OF AXIAL VELOCITY [MPH]      - if this doesnt matter choose a very high value!
Tbot = thrust_per_m_lbf                                  # BOTTOM LIMIT OF TOTAL THRUST per psu [LBF] , t/w = 3.98   - if this doesnt matter choose a very low value!
Ttop = thrust_top_m_lbf                                  # TOP LIMIT OF TOTAL THRUST per psu [LBF], t/w = 3.98   - if this doesnt matter choose a very high value!
#hover Thrust per psu =  0.6062712210084201 lbf
#Tbot_hov = 0.61                             # BOTTOM LIMIT OF hover THRUST per psu [LBF], t/w = 1    - if this doesnt matter choose a very low value!
Tbot_hov = thrust_per_m_lbf # uses bottom thrust limit                # BOTTOM LIMIT OF hover THRUST per psu [LBF], t/w = 1    - if this doesnt matter choose a very low value!
Ttop_hov = 15                               # TOP LIMIT OF hover per psu [LBF], t/w = 1  - if this doesnt matter choose a very high value!
prop_number = 15                            # number of propellers used for analysis (4 means it will select the top 4 props from the dat name file)
#prop_number = 520 # uses ALL props - based on line 61 

### should Tbot_hov as Tbot


    #### PROP FILTER 2 PARAMETERS ####
com_rpm_bot = 0                            # bottom RPM limit used for FILTER 2  - if this doesnt matter choose a very low value!
com_rpm_top = 100000                         # top RPM limit used for FILTER 2 - if this doesnt matter choose a very high value!
com_tw_bot = 1.5                           # bottom t/w limit used for FILTER 2  - if this doesnt matter choose a very low value!
com_tw_top = 10                             # top t/w limit used for FILTER 2 - if this doesnt matter choose a very high value!

################## -----END PROP RELATED-------#############################
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

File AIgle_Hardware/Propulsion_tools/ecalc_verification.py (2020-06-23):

import os
import numpy as np
import pandas as pd
import re
from io import StringIO
from IPython.display import display
import matplotlib.pyplot as plt
from mpl_toolkits.mplot3d import Axes3D
# obtaining paramters from parse file - 6 inch
'''
from parse_dat_files import DUOS_main
from parse_dat_files import MATCH_keys_df
from parse_dat_files import mass_estimate
from parse_dat_files import T_W_REQ
from parse_dat_files import T_W_toplim
from parse_dat_files import eta_motor
from parse_dat_files import eta_bat
from parse_dat_files import FT
from parse_dat_files import FT_idle
from parse_dat_files import I_dry
from parse_dat_files import v_free
from parse_dat_files import max_tilt
from parse_dat_files import n_motors
'''
# for 5 inch
from parse_dat_files5in import DUOS_main
from parse_dat_files5in import MATCH_keys_df
from parse_dat_files5in import mass_estimate
from parse_dat_files5in import T_W_REQ
from parse_dat_files5in import T_W_toplim
from parse_dat_files5in import eta_motor
from parse_dat_files5in import eta_bat
from parse_dat_files5in import FT
from parse_dat_files5in import FT_idle
from parse_dat_files5in import I_dry
from parse_dat_files5in import v_free
from parse_dat_files5in import max_tilt
from parse_dat_files5in import n_motors



#scikit for regression
# ENSURE THAT THE VERIFICATION FILE HAS THE RIGHT ORDER (BEST TO WORST MATCH) FROM LEFT TO RIGHT IN THE EXCEL FILE!
#%%##### PARAMETERS  #################
    # notes
# incorporate flight time idle as seconds of full!
# should be give an estimate of eta_full? e.g. 60% can we reason this?
#FT_eff = capa_thres*eta_bat*3600/(1000*current_thres)
# thrust to weight uses bottom limit(REQ!) -> IS THIS CORRECT
#%%#### OBTAINING ECALC VERIFICATION DATAFRAMES #############
veri_data = pd.read_excel("ECALC_test5in.xlsx", header = 3, nrows= 93)         # Import Excel File with all the data
clist = (list(veri_data))[2:] # list of configurations
n_configs = len(clist) # amount of configurations
clist.insert(0,'Property')
clist.insert(1,'unit')
complist = ['BATTERY','CONTROLLER','Accessories','MOTOR@max','MOTOR@hover','DRIVE','MULTICOP'] # list of components - seperate dataframe will be made for these
skiplist= ['oz','W/lb','mph','mi','ft/min','in²','°F','oz/W','@'] # list of all things that should be skipped when found
check =  veri_data[clist[2]] # defines column used to check database
start_c = 1 # start at 1 because 0 is a row of nans
comp_dct = {}
for j in range(0,len(complist)):
    vdata_main = pd.DataFrame(columns = veri_data.columns)
    for i in range(start_c,len(check)):
        if pd.isna(check[i]) and pd.isna(check[i+1]) and i != 47: # double nan - start new dataframe - irregular gap at index 47!
            start_c = i+3 # makes sure loop is not started at beginning again
            break
        elif veri_data['Unnamed: 1'][i] in skiplist: # gets rid of rows unit in skip list
            pass
        else:
            veri_row = veri_data[i:i+1]
            vdata_main = pd.concat([vdata_main,veri_row],ignore_index = True)      
    vdata_main.columns = clist # renames columns 
    comp_dct[complist[j]] = vdata_main
print('------- DONE WITH ECALC DATAFRAMES---------')
#%%## COMPARING VERIFICATION DATA TO OWN TRIPLETS! ###
# comparison occurs by comparing verification data with own in (new-old)/old -> old = veri data!
#DUOS_main = own data results
#MATCH_keys_df = keys req to acces duos_main
### ABSOLUTE & RELATIVE ERROR DEFINITIONS ### 
def error_r(a,b): # relative error
    error_r = (float(a)-float(b))/float(b)*100 # in percentage
    return(error_r)
def error_a(a,b): # absolute error
    error_a = float(a)-float(b)
    return(error_a)

### COMPARING MOTOR AT 100% ###
verimotor_df = comp_dct['MOTOR@max']  # motor at 100%
veribat_df = comp_dct['BATTERY']  # battery related dataframe
vericonfig_df = comp_dct['MULTICOP']  # general config related dataframe - last part of excel
veridrive_df = comp_dct['DRIVE']  # drive related dataframe
mveri_results_2c = [['m Weight[g]','abs'],['m Current[Amp]','%'],['m Voltage[V]','%'],['m RPM[rev/s]','%'],['m Input power[W]','%'],['m Efficiency[%]','abs']] # first two columns of motor results df
mveri_results_df = pd.DataFrame(mveri_results_2c, columns = ['Property','rel or abs?']) # dataframe for motor results 
start_r = 0 # defines starting point - ensures duplictation will not occur
### COMPARING GENERAL CONFIGURATION PROPERTIES ###
#totveri_results_2c = [['Total Weight[g]','%'],['T/W','%'],['Overall efficiency','%'],['Max tilt angle','%'],['Max speed','%'],['Flight time @max','abs']] # first two columns of results df
totveri_results_2c = [['Total Weight[g]','%'],['T/W','abs'],['Max tilt angle [°]','abs'],['Max speed','%'],['Flight_time@max[sec]','abs']] # first two columns of results df
totveri_results_df = pd.DataFrame(totveri_results_2c, columns = ['Property','rel or abs?']) # dataframe for general config results
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

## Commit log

2020-06-02 added prints to ease readbility
2020-06-23 Added catia files and renders
    [BATTERY_DATABASE.xlsx, ECALC_finalconfig.xlsx, ECALC_test5in.xlsx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]
2020-06-23 added renders 2
    [1.0.CATPart, 2.0.CATPart, 30..CATPart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]
2020-06-23 removed airsim demo, added docu preview
    [params.txt]
2020-06-23 added pcb info
    [1.0.CATPart, 2.0.CATPart, 30..CATPart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]
2020-06-23 added render pic
    [AIgle_Carrier_Board.PrjPcb, IO_Connector.SchDoc, Power_Logic.SchDoc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]
2020-06-23 fix commit
    [AIgle_Carrier_Board.PrjPcb, IO_Connector.SchDoc, Power_Logic.SchDoc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]
2020-06-28 added samacsys library loader files
    [SamacSys.PcbLib, SamacSys.SchLib]
2020-07-02 Create 3D print STL files
2020-07-02 Create stl files
2020-07-03 Rename 3D print files ./1x_Camera.stl to 3D print files/1x_Camera.stl
    [1x_Camera.stl]
2020-07-03 organised repo
    [1.0.CATPart, 2.0.CATPart, 30..CATPart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]
